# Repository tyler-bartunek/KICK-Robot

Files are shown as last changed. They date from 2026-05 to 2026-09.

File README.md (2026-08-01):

# The KICK Robot KICK Logo

&nbsp;
&nbsp;
_Democratizing robotics, one shoebox at a time_

The KICK (Kinematically Interchangeable Control Kit) Robot framework is an open-source platform designed to make learning about and development of mobile robotic systems accessible, modular, and affordable.

## Table of Contents
- [Repository Structure](#repository-structure)
- [The Wiki](#the-wiki)
- [Module Descriptions](#module-descriptions)
- [Hardware](#hardware)
  - [Printed Components and Module Fit](#printed-components-and-module-fit)
- [Future development](#future-development)
- [FAQ](#faq)
- [License](#license)

## Repository Structure
- `/hardware/` – STL and STEP files for 3D printing
- `/software/` – Code for the centralized controller (in progress), example firmware for modules, and hardware test scripts
- `/docs/` – Printing instructions, and additional reference material as it becomes available (PDF)
- `/images/` – Holds images used in this README, as well as some others throughout the repository
- `README.md` – You are here.

## The Wiki
Documentation for this project, including: 

- Part orientation and printer setting recommendations
- Assembly instructions
- Calibration and hardware validation protocols
- System-level descriptions
- and more

are being migrated to the [project wiki](https://www.github.com/tyler-bartunek/KICK-Robot/wiki) for ease of access
and navigation purposes. There's a lot that goes into this system, and it is only fitting that worthy documentation
would be quite extensive, requiring a wiki to track it all. 

## Module Descriptions
Here are a few of the modules under development at present for the KICK Robot. Once these modules are fully fleshed
out, a homebrew guide will be produced and added to the wiki.

1. Wheels: This module consists of DC motors and mecanum wheels, represents minimal functional example (systems integration in process).
2. Shoeshine: Offers quadrupedal motion through use of servomotors (Pending Initial Design)
3. HexaBox: Requires six mounts, offers six-legged locomotion through use of servomotors. (Pending Initial Design)

Note that each module type gets its own uint8_t identifier. Here are some urrently used ID's within KICK framework:

| ID | Module Type |
|----|---|
|0x00 | **Reserved**: No Connection |
|0x01 | Echo test functionality |
|0x02 | Mecanum Wheel Version A |
|0x03 | Mecanum Wheel Version B |
|0x04 | Quadruped Leg Version A |
|0x05 | Quadruped Leg Version B |

## Hardware

### Printed Components and Module Fit
Both STEP and STL files for all components to be printed are provided under the hardware directory, with directions for
the base hardware and wheels module provided in the wiki. As modules are added, printing directions specific
to those modules will be added. This system was prototyped using an Ender 3 V2 and Cura slicer using 
PLA+, with dimensions set to reflect typical tolerances for that printer with the intent of clearance fits with minimal play between 
mounting rails and modules.

## Software
Files for characterizing your specific motors and verifying basic hardware connections to the Pi, such as the ADC for 
battery level monitoring and custom SPI fanout board PCB, are provided within this repository, as well as the base
code for the picos/modules. Module code was developed using the Raspberry Pi Pico C++ SDK and uses CMake (C++17).

ROS code for the Raspberry Pi was developed using the ros:jazzy-core docker image, and is available on a [separate repository](https://github.com/tyler-bartunek/kick_pi) for direct download on your raspberry pi once finished. Raspberry 3b+ or better strongly encouraged, as the project was developed on a 3b+. 

### Philosophy, Parent Classes: Validation Ongoing, wiki articles available upon completion
While this is explained in greater detail in the [wiki](https://www.github.com/tyler-bartunek/KICK-Robot/wiki), provided here is a brief overview
for integration purposes. Overall, the goal is for users to be able to extend this framework to arbitrary module configurations. 

#### Configuration Class (ROS)
Within this project's underlay (not to be confused with the ROS underlay), there is a kickbrain package. This package has a nested package within it
called "configuration_files". The Configuration class is defined within this subpackage, and all kinematic calculations are predicated on the geometry_msgs.msg.Twist message type coming from the motion planner, with these velocities defined relative to the center of mass, presumed or actual. 

**All user-defined configurations must inherit from the Configuration parent class and have both a fetch_commands and compute_received method defined as following signatures:** 
```
def fetch_commands(self, vel_cmd: Twist, feedback) -> list:
```

This method takes the center of mass velocity command from the motion planning node, which uses the built-in geometry\_msgs.Twist topic message type and any feedback to compute new actuator commands. 

``` 
def compute_received(self, device_data) -> Twist:
```
This method takes the data received from the bus\_hub node and computes the forward kinematics for your configuration to build feedback. 

Once you have your configuration kinematics defined, you go to the \_\_init\_\_.py file within the configuration\_files directory and add the frozenset of module ids that can be used to recognize your configuration. Note that it does use a frozenset, so if you need X number of modules for a successful deployment, be sure to add that check to your custom configuration's class definition.

__**Note that 0x00 is reserved as the "no connection" module ID, so your frozenset will need to include it if any connection points on the harness are disconnected**__

_There is a possibility that you will need to modify it directly within the kickbot_node package and rebuild it using colcon build --packages-select to achieve desired behavior, but efforts will be made to allow you to develop your own configuration definitions in an overlay._

#### Module Class (Pico)
The microcontroller code for the picos is organized in the following folder structure:

1. kick_pico: **project root, make/build from here** <br>
   a. modules: Contains the Module parent class and any subclass definition cpp and h files <br>
   b. utils: Additional cpp and header files for achieving any functionality the modules require, such as SPI communication or quadrature encoder reading <br>
   c. main.cpp: driver script, creates the `pico_device` instance and calls its `run()` method repeatedly <br>

You define your custom module by adding a header and cpp file within the modules subdirectory, and be sure to add the relevant files to the CMakeLists.txt file within that subdirectory. The custom module class that you define **must** inherit from the Module base class, and must include a run method override that defines your module's behavior in response to received data from the Pi. That run method **must** call `this -> Transfer(data)`, where `data` is a short (uint16\_t) being sent back to the pi. 

Minimally viable example of a custom subclass header file:
```
#pragma once

#include "Module.h"

class MinimalExample : public Module {
    
    public:
        
        MinimalExample();

        void run() override;

        ~MinimalExample() = default;
};
```

If your module requires additional custom header files to function, these go under the utils subdirectory and you will in turn need to modify that CMakeLists.txt file.

For example, if you need to add something for the module to read an encoder that you've either written or cloned a library for named MyReallyCoolEncLib, you would modify the very first line of CMakeLists.txt file in utils to read:

```
add_library(utils STATIC SPITools.cpp MyReallyCoolEncLib.cpp)
```

assuming that your library has a cpp file defined for it.

Lastly, you modify line 18 of main.cpp to have the name of your new module type

```
#define MODULE_TYPE MinimalExample
```

**When you define your own module definitions they must inherit from the Module base class, have a unique uint8_t ID defined, and contain a run() method override.** A sync_callback() method override is optional, but recommended if the modules need to act in a coordinated fashion (as most do). Wiki article coming soon.  

## Future development
This project is still under development, and additional details such as synchronization and timing
requirements will be made available as they are validated. Current work is focused on validating the ROS setup and getting the Wheels Module ready to ``roll". 

## FAQ

1. Why shoeboxes?

>I had originally set out to make what essentially amounts to just the wheels module as a CAD and mechatronic portfolio piece.
Seeking to understand the design considerations, I started to immerse myself in literature surrounding mecanum wheel devices 
and discovered something that is in hindsight self-evident: different design decisions like the wheel spacing and orientation 
fundamentally alters the dynamics of the system and therefore influence control. Creating modular systems to explore the impact 
of these parameters was largely underexplored in what I found, so I set out to make my own. But I needed a good frame. Something
cheap and easy to deploy. As I looked around me, I saw an unused shoebox. And the KICK Robot was born. 

>Realistically any cardboard box will work, but at the time a shoebox seemed like the right size for what I set out to accomplish.

2. Why didn't you use \<insert fastener here\> to fasten the modules to the box?

>In the early days, I explored a number of different means for mounting the hardware to the box. The current design for mounting
hardware to the box solves two problems simultaneously: the first is that of establishing a secure connection with minimal
assembly complexity, the second is offering a path for routing the wires from inside the box to the modules on the outside.

3. Doesn't the act of cutting into the box limit the reusability of a single box to test multiple design parameters?

>Yes, as do other adhesives that have enough strength to reliably anchor the hardware to the outside of the box. 

## License
As of 19 November, 2025, this project is licensed under the terms of the [Apache License-2.0](LICENSE). Software provided prior 
to this date was licensed under the terms of the MIT license, and includes the content of the directory 
`/software/Hardware Characterization/Wheels Module`. The transition to the Apache License-2.0 is to reflect that this repository
contains more than just software. 

This project also uses PyMC in the motor characterization code for the Wheels module. PyMC is also licensed under the terms
of the [Apache License-2.0](LICENSE), and also includes software licensed under the MIT license. A notice is provided in the
main directory of this repository, to underline this point and include the necessary copy of the MIT license for portions 
covered by that license.

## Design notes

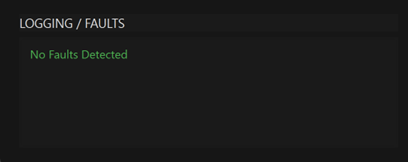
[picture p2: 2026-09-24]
images/wiki/KICK-GUI-logging.png

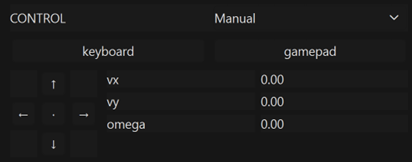
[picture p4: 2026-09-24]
images/wiki/KICK-GUI-control.png

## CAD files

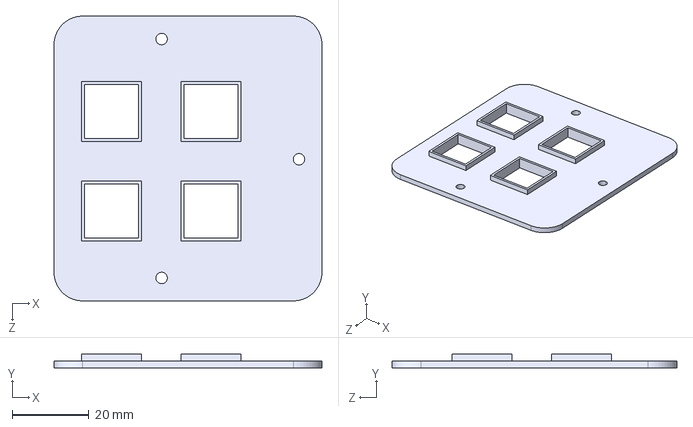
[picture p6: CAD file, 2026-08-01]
Hardware/Attachment Points/STEPs/BasePlate_Ext_Middle.STEP
70.0 x 3.60 x 74.4 mm

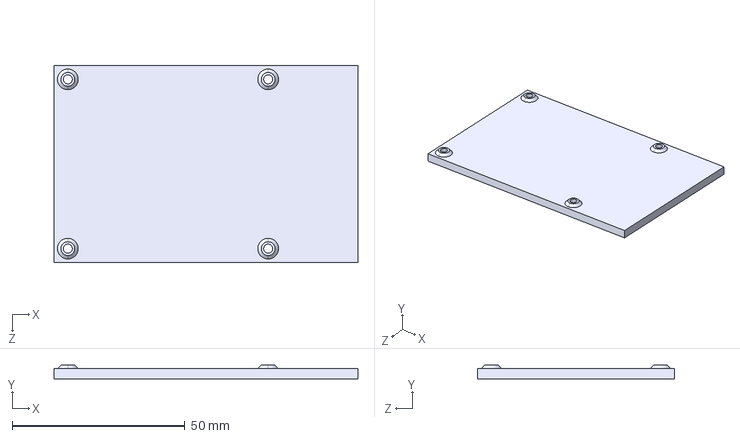
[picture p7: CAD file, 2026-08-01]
Hardware/Central Electronic Mounts/STEPs/Rpi_3b_mount.STEP
88.0 x 4.00 x 57.0 mm

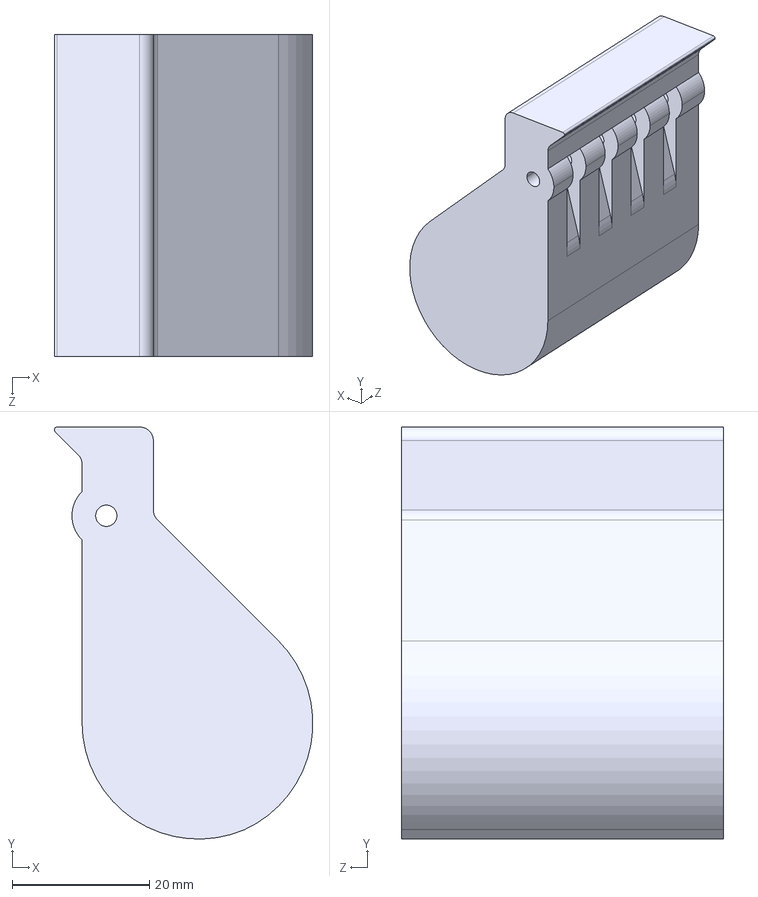
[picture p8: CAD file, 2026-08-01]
Hardware/Wheel Module/STEPs/Handle.STEP
37.6 x 60.1 x 47.0 mm

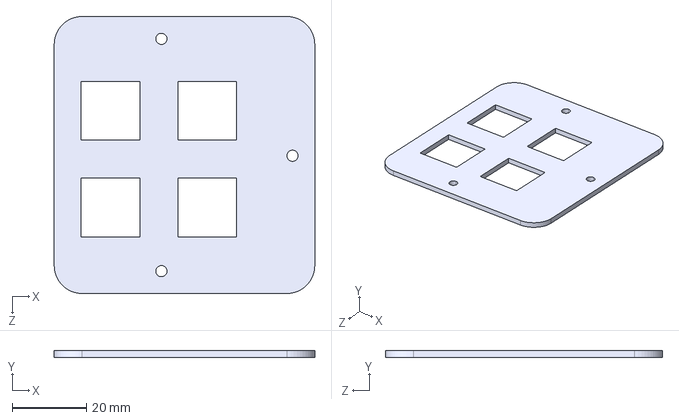
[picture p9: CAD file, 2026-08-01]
Hardware/Attachment Points/STEPs/BasePlate_Int_Middle.STEP
70.0 x 1.80 x 74.4 mm

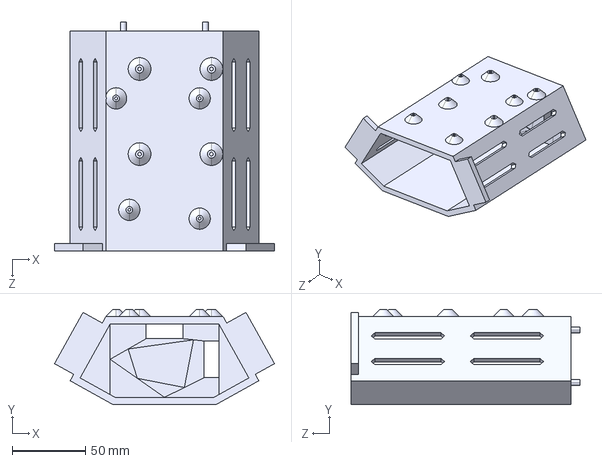
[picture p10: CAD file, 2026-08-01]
Hardware/Central Electronic Mounts/STEPs/Central_Electronics_Mount.STEP
150.0 x 65.0 x 156.0 mm

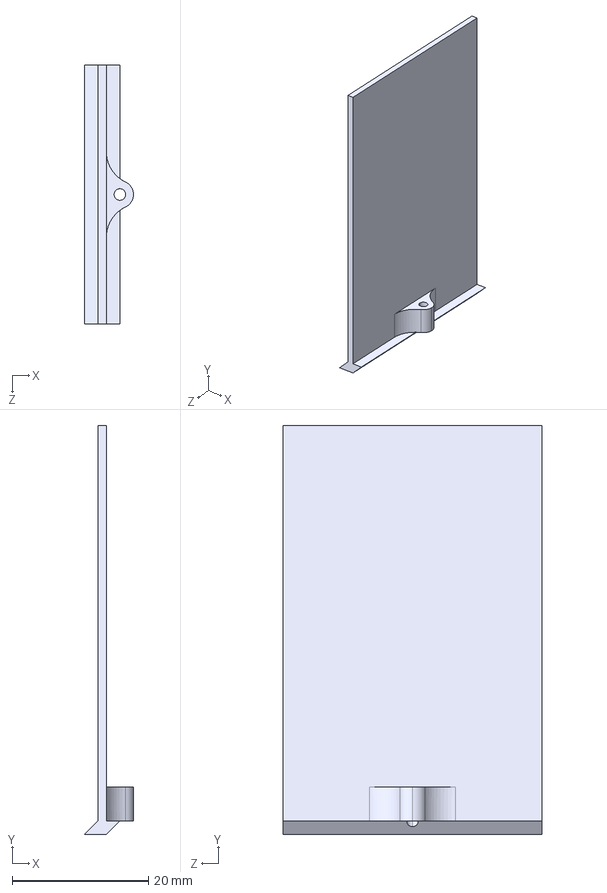
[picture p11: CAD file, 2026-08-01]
Hardware/Wheel Module/STEPs/Pico_Shield.STEP
7.20 x 60.0 x 38.0 mm

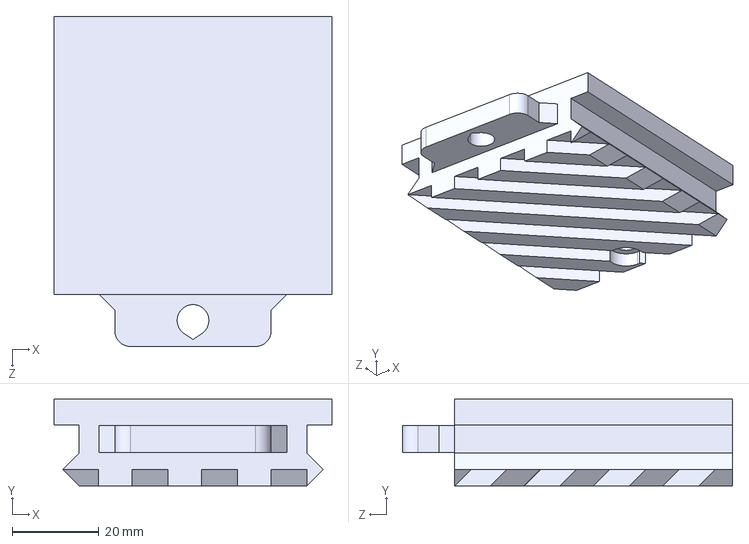
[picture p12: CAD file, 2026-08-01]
Hardware/Attachment Points/STEPs/BaseMount.STEP
64.0 x 20.0 x 76.0 mm

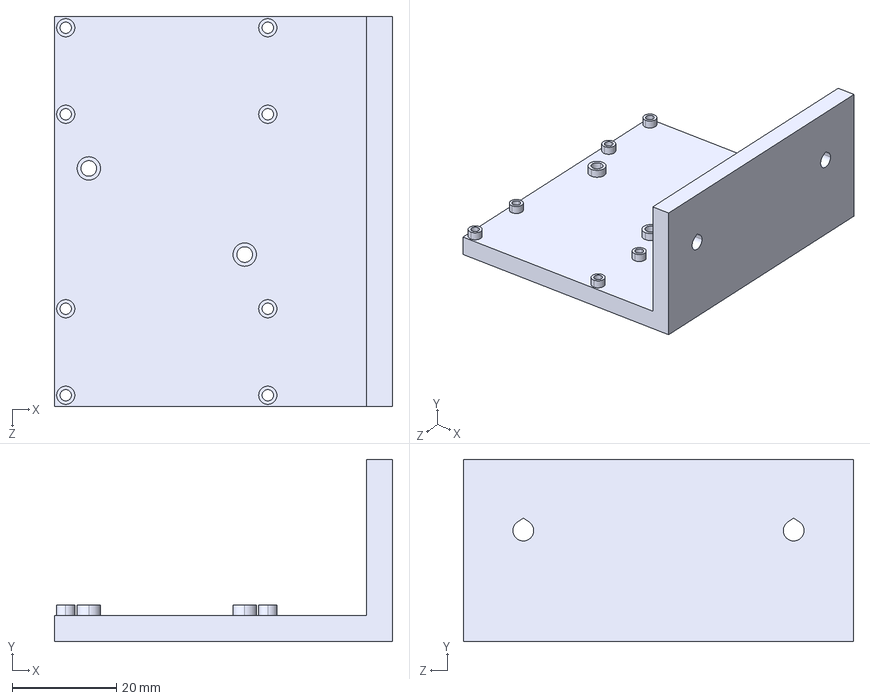
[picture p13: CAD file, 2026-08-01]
Hardware/Central Electronic Mounts/STEPs/Buck_Mount.STEP
65.0 x 35.0 x 75.0 mm

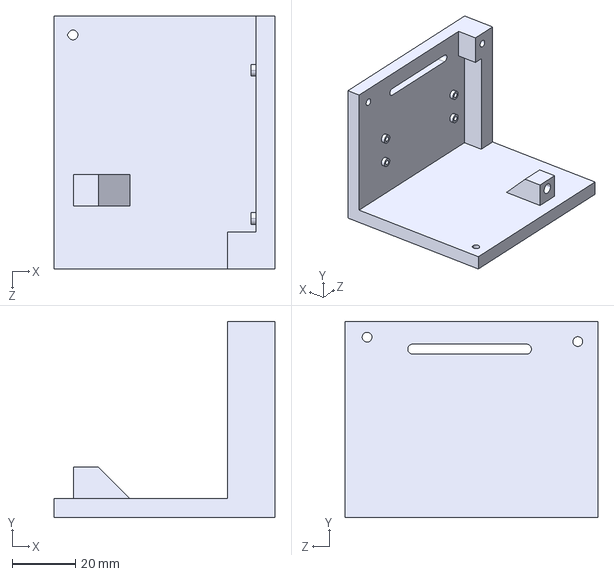
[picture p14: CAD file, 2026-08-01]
Hardware/Wheel Module/STEPs/Motor_Mount_Side_Bottom.STEP
70.0 x 62.2 x 80.2 mm

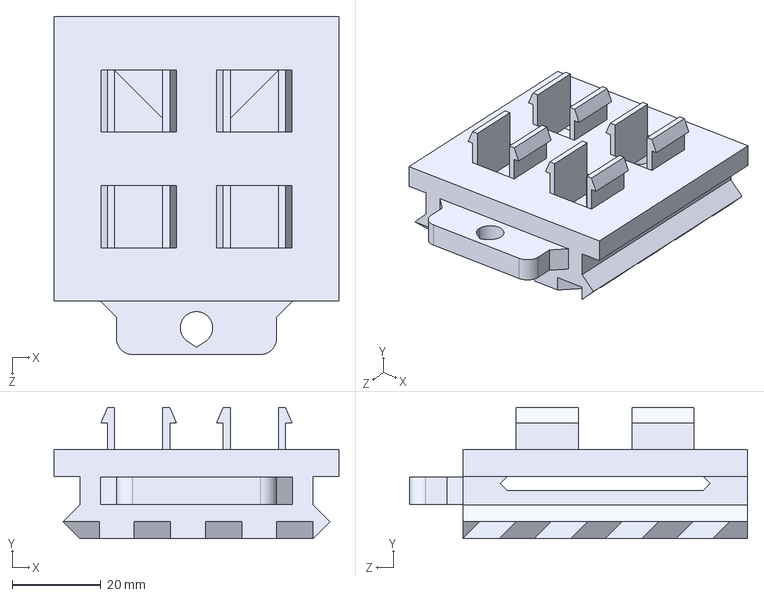
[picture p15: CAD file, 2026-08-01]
Hardware/Attachment Points/STEPs/BaseMount_Clips.STEP
64.0 x 29.5 x 76.0 mm

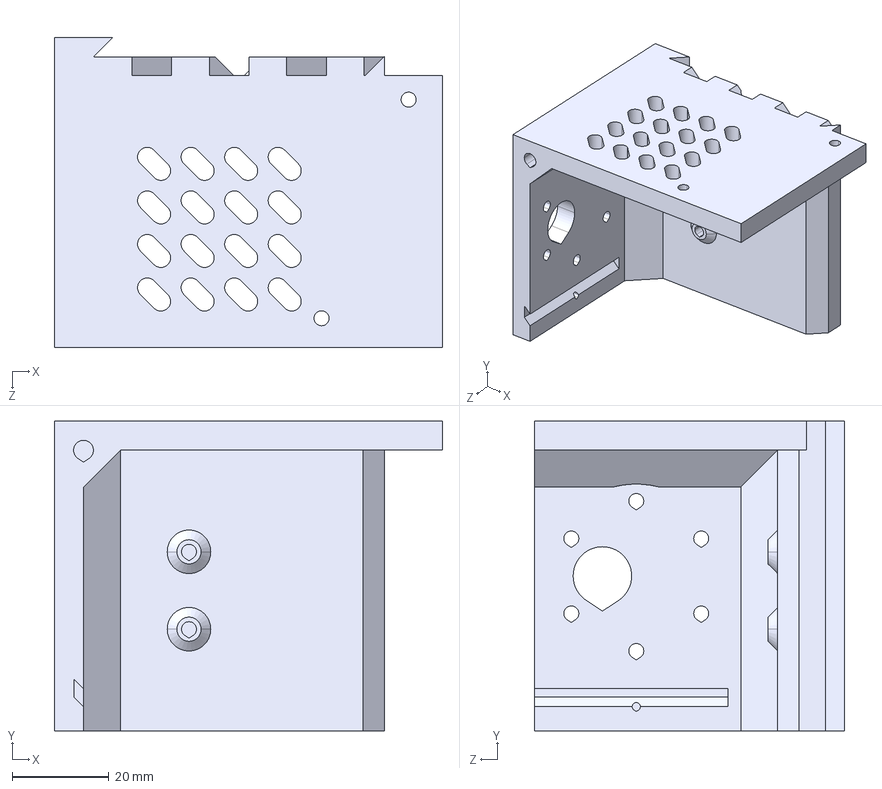
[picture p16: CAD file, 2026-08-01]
Hardware/Wheel Module/STEPs/Motor_Mount_Attachment.STEP
80.2 x 64.0 x 64.0 mm

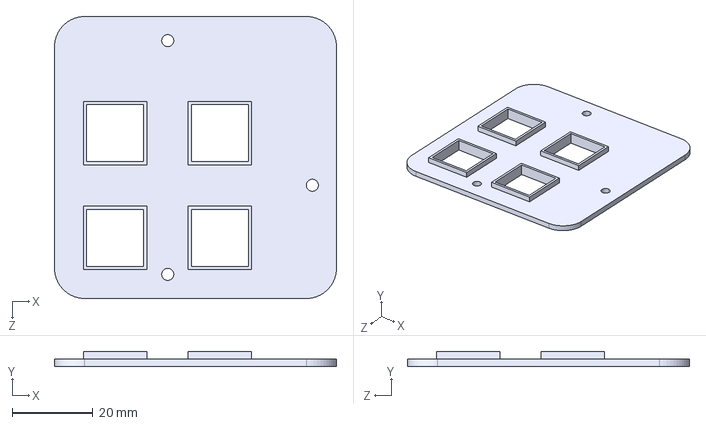
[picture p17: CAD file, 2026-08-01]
Hardware/Attachment Points/STEPs/BasePlate_Ext_Corner.STEP
70.0 x 3.60 x 70.0 mm

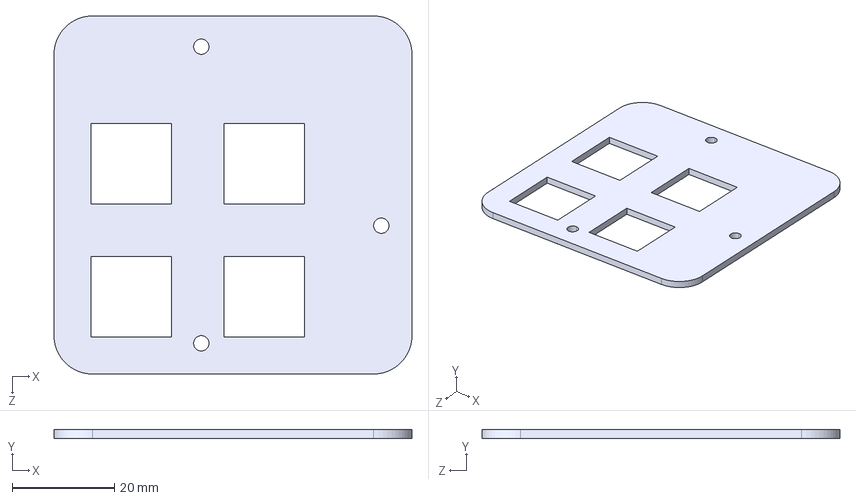
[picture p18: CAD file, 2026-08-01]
Hardware/Attachment Points/STEPs/BasePlate_Int_Corner.STEP
70.0 x 1.80 x 70.0 mm

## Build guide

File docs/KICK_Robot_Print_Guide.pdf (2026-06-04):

# KICK Robot

# Quick-Start Excerpt: Printing Guide

## Revision Date: June 3, 2026

# Contents

## Downloading Files

These instructions are written for a Windows 10 computer, though the basic principles should transfer reasonably well to other platforms like Mac and Linux operating systems.

## Installing Git

Open a web browser and navigate to https://git-scm.com/ and go to the downloads page. Follow their posted directions, and once installation is complete you will be ready to get started.

## Cloning the Repository

Once git is installed, open a terminal and navigate to the directory where you would like to save the project files. If you know how to do this already, you can skip the steps detailing this process.

### Navigating to Desired Directory using Command Prompt

You do this on Windows by going to the search bar and typing “cmd”, you should see something like the following come up, though the specifics will depend on the software you have installed on your device.

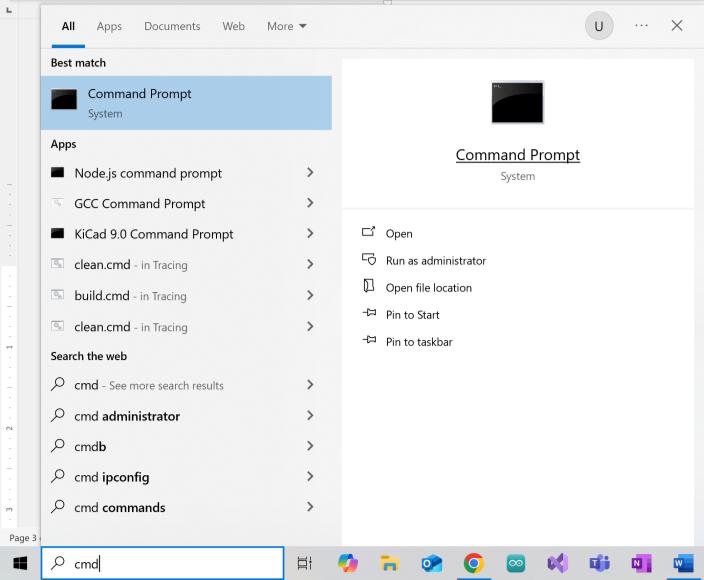
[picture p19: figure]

Figure 1. This screenshot illustrates opening the Command Prompt terminal from the Windows search bar.

1. Open Command Prompt and you should see a terminal window open. Odds are good that your desired location is going to be somewhere off the user directory, which is what Command Prompt opens to by default. In this example, the desired directory is a desktop folder created specifically for the user’s GitHub repositories.

2. Type cd ./<name of target directory> In the example provided in Figure 2, the full command is cd ./Desktop/My Stuffs/Git Repos/

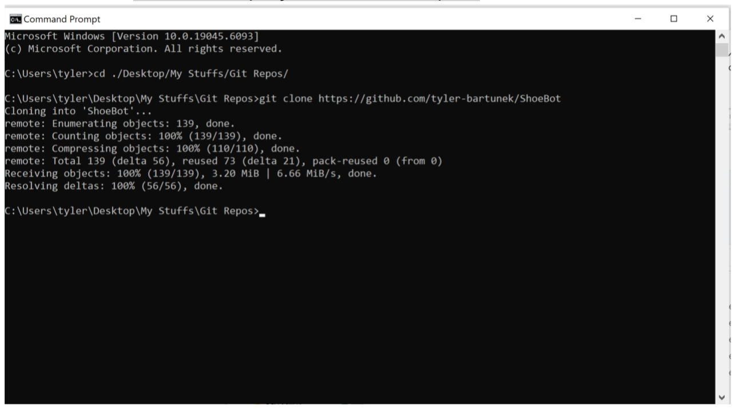
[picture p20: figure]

Figure 2. The complete set of commands necessary to get a clone of the repository onto your local device. The repository has been renamed since this was generated, disregard the ShoeBot mention.

### Finally Cloning the Repository

Now that you are set up with git and are have navigated to the location you want the files to download, it is time to download a copy of the files into this location. Type or copy-paste

git clone https://github.com/tyler-bartunek/KICK-Robot

into your terminal. The download process should run automatically and once finished you should have a new folder in that location named KICK-Robot. Note that it may prompt you to sign in to github, which may entail setting up an account.

If this step has finished successfully, then you can now close the Command Prompt and continue navigation through the File Explorer like usual.

## Printing Instructions for Hardware

Navigate to the Hardware directory of the repository. In it, you will find folders for

- Attachment Points
- Central Electronic Mounts

- SPI Hub PCB KiCad files
- Wheel Module.

This section will concern all of these folders except the SPI Hub folder, as that information is for an optional component that is not 3D-printed. Every folder that has parts to be 3D-printed will contain folders for STEP and STL files, with the former provided in the event that you need to modify the base design of any of the components.

All parts were printed using PLA+ during the design process with:

- 0.4 mm nozzle and line width
- 20% infill (cubic)
- Tree supports as applicable
- 2 wall lines
- 50 mm/s print speed

To maximize print time efficiency, it is strongly recommended to print multiple components at once. For example, printing half of the rail pieces in a batch and all the motor mount attachments in another batch instead of each rail and motor mount attachment piece individually. With these print settings it was not uncommon to encounter 2+ day prints on an Ender 3V2 running Marlin. So again, the recommendation is to print as many things simultaneously as possible.

In total, you will need to print the following to match the development setup:

- 6 Base Mount Clips
- 4 Base Mounts
- 4 Internal Corner Plates
- 2 Internal Middle Plates
- 4 External Corner Plates
- 2 External Middle Plates
- 4 Motor Mount Attachments
- 4 Motor Mount Side Bottoms
- 4 Handles
- 4 Pico Shields
- 1 Central Electronics Mount
- 1 Buck Converter Mount
- 1 Raspberry Pi 3b+ Mount
- 4 Spacers (print last)

For best results, print at a 0.1 mm layer height as this will allow in Cura for steeper overhangs and fewer supports.

## Attachment Points

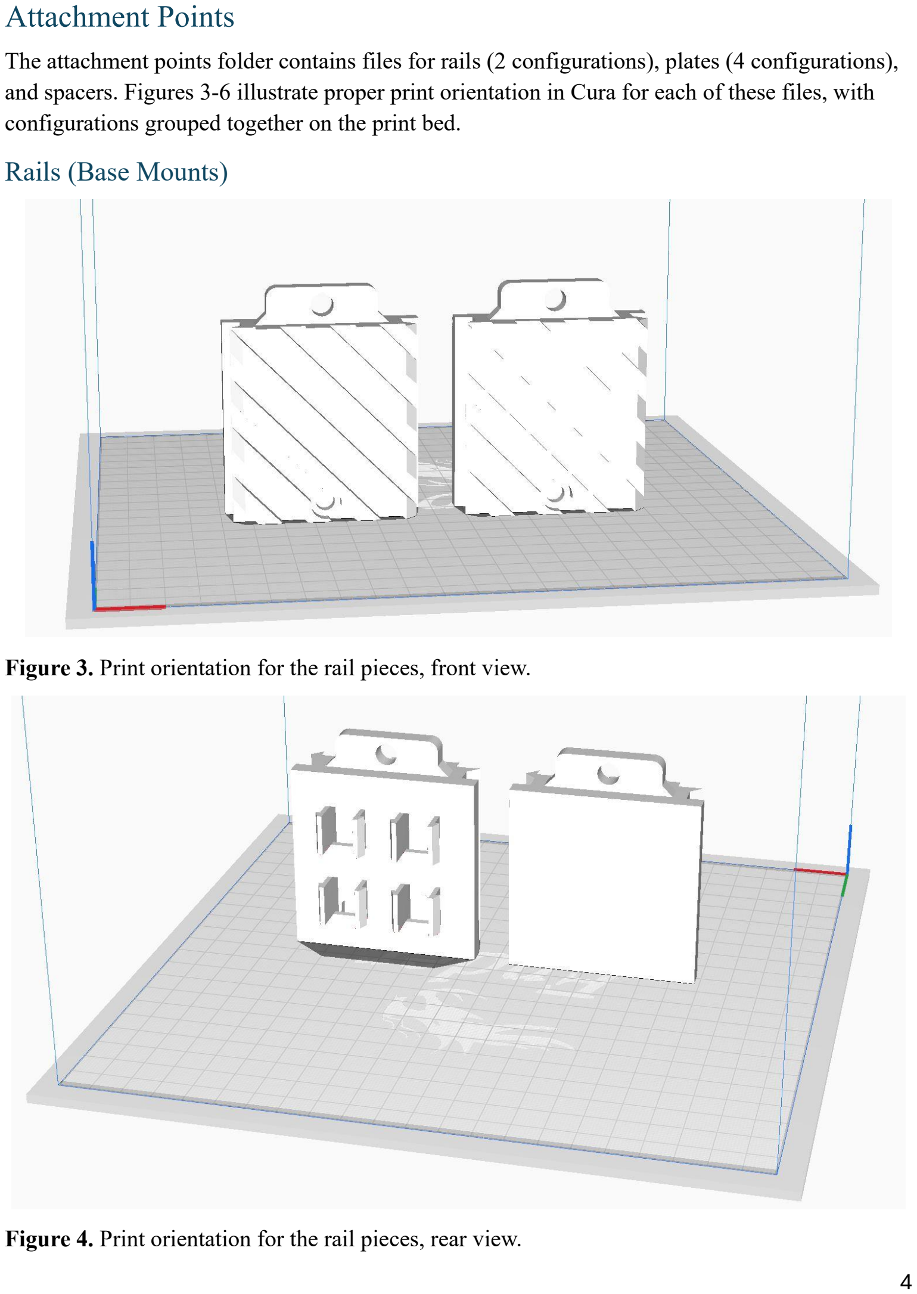
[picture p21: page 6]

The attachment points folder contains files for rails (2 configurations), plates (4 configurations), and spacers. Figures 3-6 illustrate proper print orientation in Cura for each of these files, with configurations grouped together on the print bed.

### Rails (Base Mounts)

Figure 3. Print orientation for the rail pieces, front view.

Figure 4. Print orientation for the rail pieces, rear view.

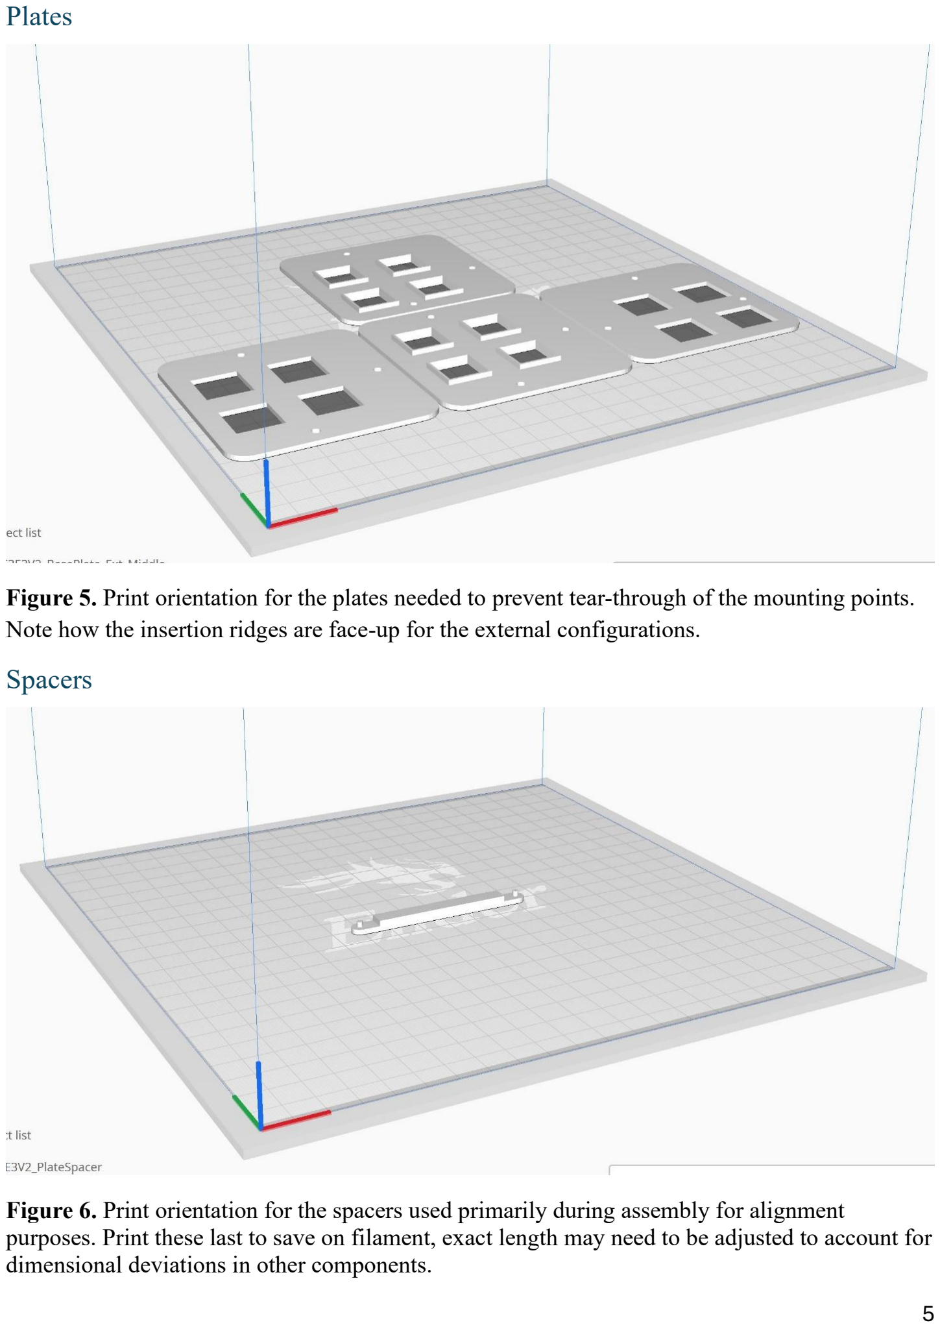
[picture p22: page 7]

### Plates

Figure 5. Print orientation for the plates needed to prevent tear-through of the mounting points. Note how the insertion ridges are face-up for the external configurations.

### Spacers

Figure 6. Print orientation for the spacers used primarily during assembly for alignment purposes. Print these last to save on filament, exact length may need to be adjusted to account for dimensional deviations in other components.

## Central Electronics Mount

### Central Mount

## Pending Redesign

Figure 7. Print orientation for the central electronics mount.

### Buck Attachment Point

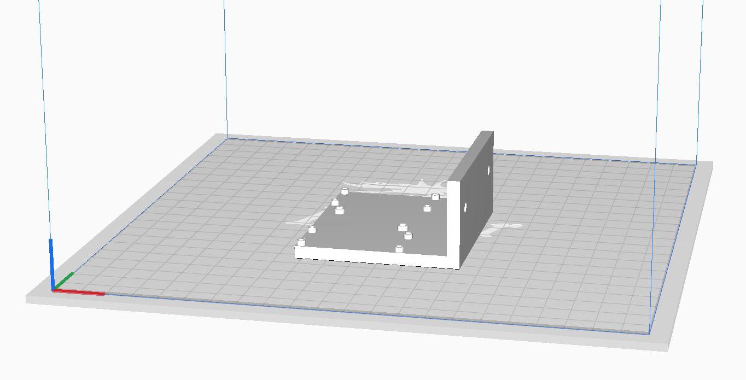
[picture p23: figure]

Figure 8. Print orientation for the buck converter mounting point, with the raised portions oriented upwards.

## Wheels Module Hardware

### Motor Mount Attachment

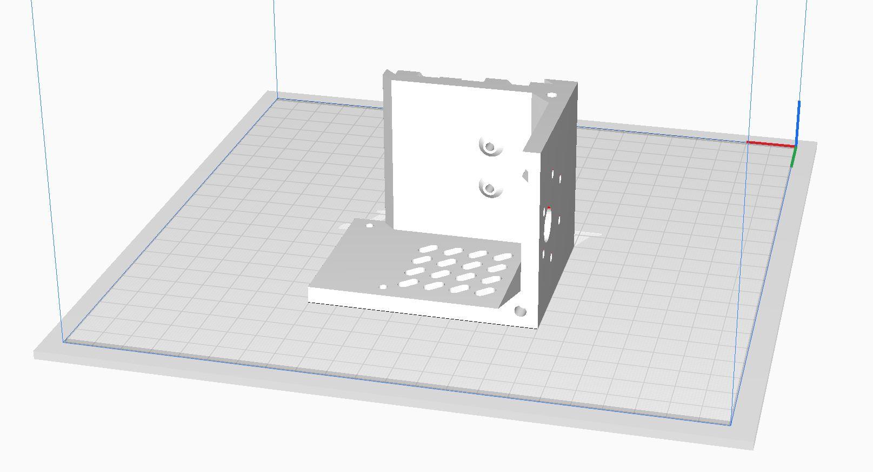
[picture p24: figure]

Figure 10. Print orientation for the motor mount attachment piece, illustrating that ventilation slots print on the bottom face.

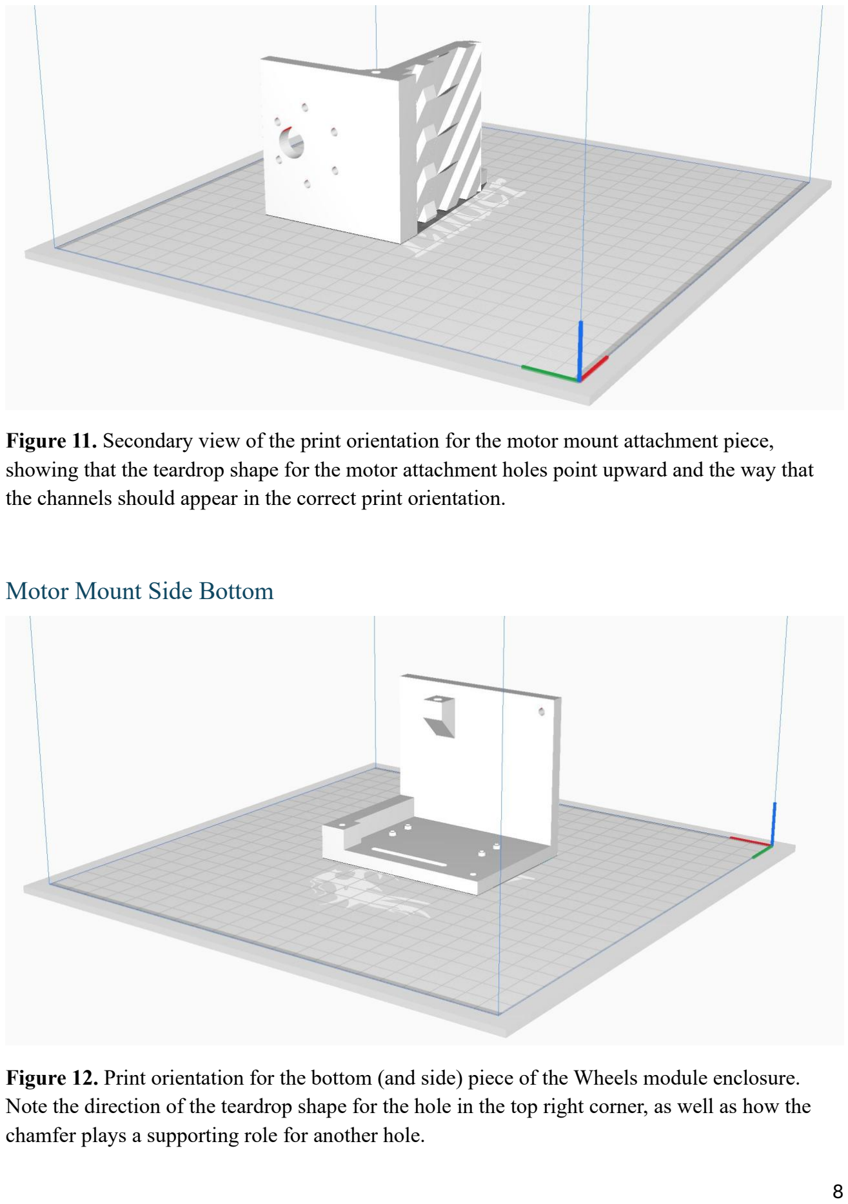
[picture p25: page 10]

Figure 11. Secondary view of the print orientation for the motor mount attachment piece, showing that the teardrop shape for the motor attachment holes point upward and the way that the channels should appear in the correct print orientation.

### Motor Mount Side Bottom

Figure 12. Print orientation for the bottom (and side) piece of the Wheels module enclosure. Note the direction of the teardrop shape for the hole in the top right corner, as well as how the chamfer plays a supporting role for another hole.

### Handle

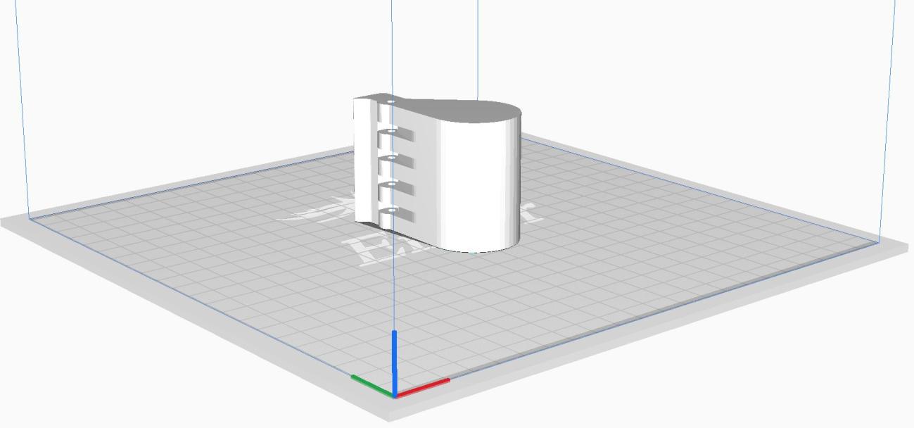
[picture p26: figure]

Figure 13. Print orientation for the handle of the wheels module. Note that care should be taken to ensure that the gaps for the springs are cleaned out well enough for the springs to fit, as supports will want to fill this space.

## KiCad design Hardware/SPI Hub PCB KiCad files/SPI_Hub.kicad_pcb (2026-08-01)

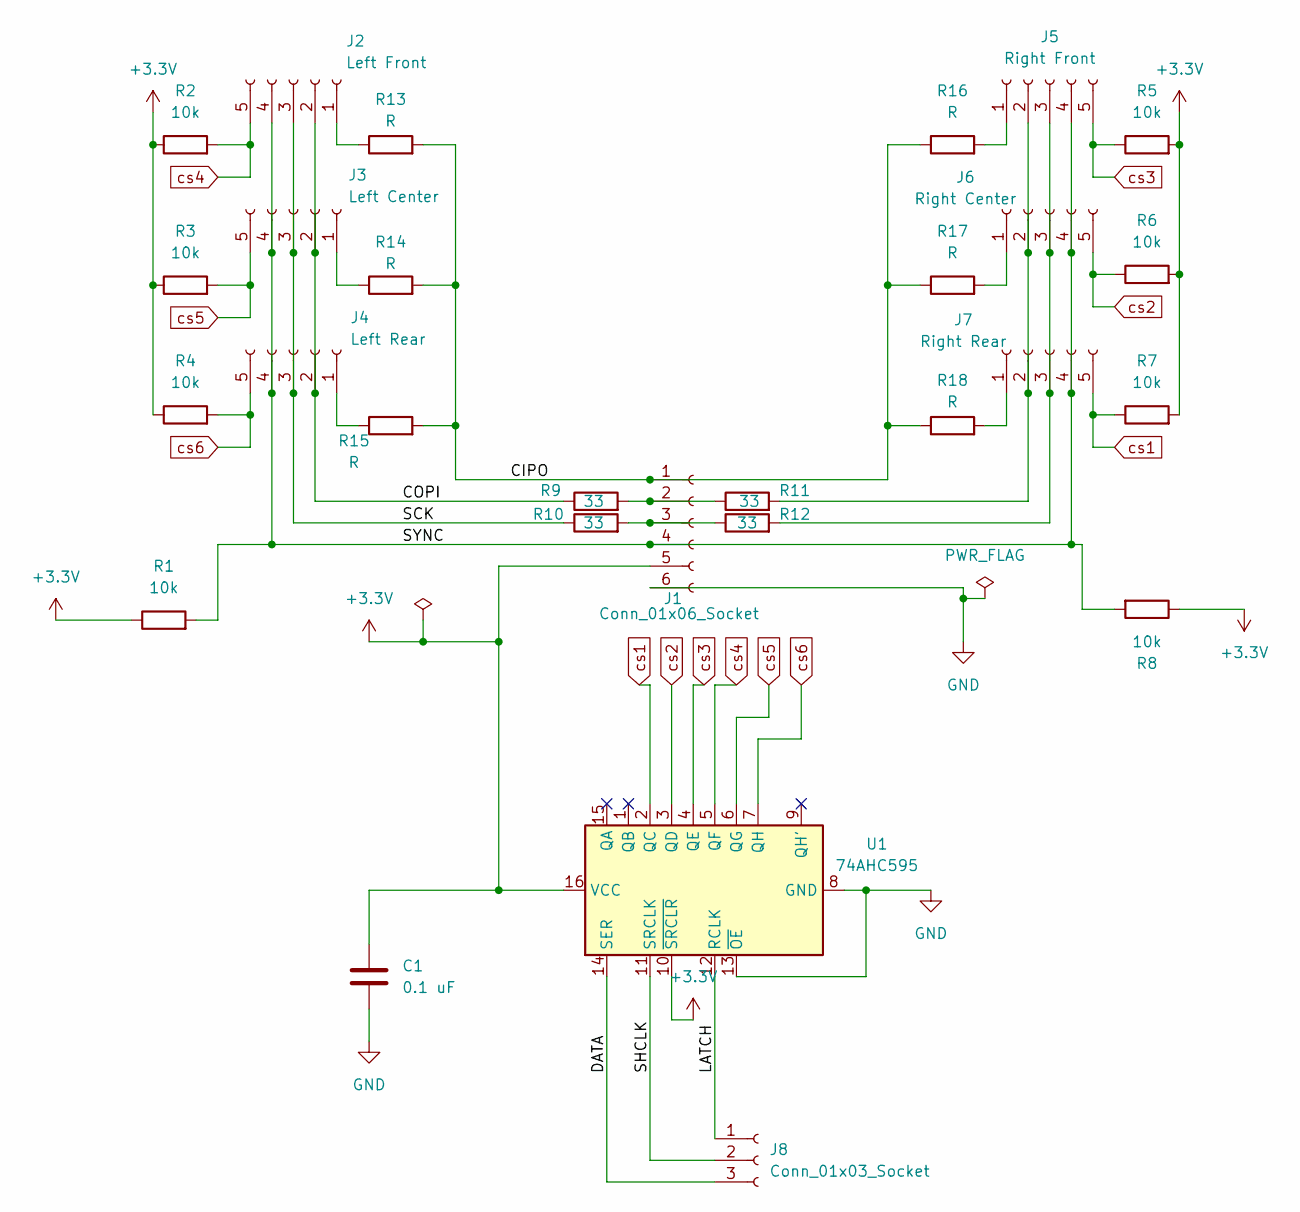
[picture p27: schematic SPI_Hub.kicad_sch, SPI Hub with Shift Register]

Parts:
C1: 0.1 uF; C_0805_2012Metric_Pad1.18x1.45mm_HandSolder
J1: Conn_01x06_Socket; JST_XH_B6B-XH-A_1x06_P2.50mm_Vertical
J2: Left Front; JST_XH_B5B-XH-A_1x05_P2.50mm_Vertical
J3: Left Center; JST_XH_B5B-XH-A_1x05_P2.50mm_Vertical
J4: Left Rear; JST_XH_B5B-XH-A_1x05_P2.50mm_Vertical
J5: Right Front; JST_XH_B5B-XH-A_1x05_P2.50mm_Vertical
J6: Right Center; JST_XH_B5B-XH-A_1x05_P2.50mm_Vertical
J7: Right Rear; JST_XH_B5B-XH-A_1x05_P2.50mm_Vertical
J8: Conn_01x03_Socket; JST_XH_B3B-XH-A_1x03_P2.50mm_Vertical
R1, R2, R3, R4, R5, R6, R7, R8: 10k; R_0805_2012Metric_Pad1.20x1.40mm_HandSolder
R9, R10, R11, R12: 33; R_0805_2012Metric_Pad1.20x1.40mm_HandSolder
R13, R14, R15, R16, R17, R18: R; R_0805_2012Metric_Pad1.20x1.40mm_HandSolder
U1: 74AHC595; DIP-16_W7.62mm_Socket

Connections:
+3.3V: C1.1, J1.5, R1.1, R2.1, R3.1, R4.1, R5.2, R6.2, R7.2, R8.1, U1.10 (~SRCLR), U1.16 (VCC)
/CIPO: J1.1, R13.2, R14.2, R15.2, R16.1, R17.1, R18.1
/COPI: J2.2, J3.2, J4.2, R9.1
/DATA: J8.3, U1.14 (SER)
/LATCH: J8.1, U1.12 (RCLK)
/SCK: J2.3, J3.3, J4.3, R10.1
/SHCLK: J8.2, U1.11 (SRCLK)
/SYNC: J1.4, J2.4, J3.4, J4.4, J5.4, J6.4, J7.4, R1.2, R8.2
GND: C1.2, J1.6, U1.8 (GND), U1.13 (~OE)
unnamed: J1.2, R9.2, R11.1
unnamed: J1.3, R10.2, R12.1
unnamed: J2.1, R13.1
unnamed: J3.1, R14.1
unnamed: J4.1, R15.1
unnamed: J5.1, R16.2
unnamed: J5.2, J6.2, J7.2, R11.2
unnamed: J5.3, J6.3, J7.3, R12.2
unnamed: J6.1, R17.2
unnamed: J7.1, R18.2
cs1: J7.5, R7.1, U1.2 (QC)
cs2: J6.5, R6.1, U1.3 (QD)
cs3: J5.5, R5.1, U1.4 (QE)
cs4: J2.5, R2.2, U1.5 (QF)
cs5: J3.5, R3.2, U1.6 (QG)
cs6: J4.5, R4.2, U1.7 (QH)

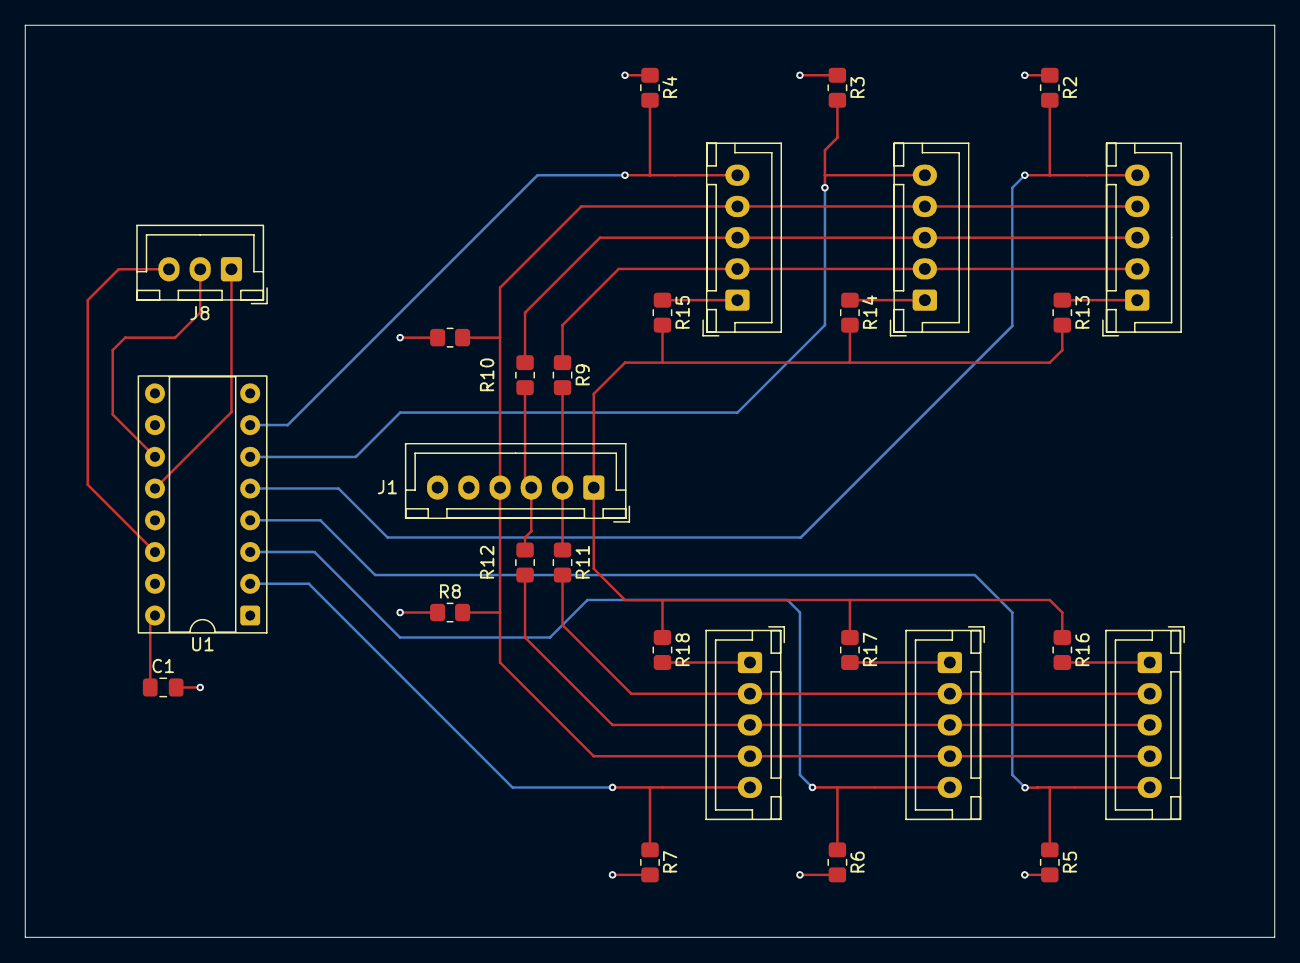
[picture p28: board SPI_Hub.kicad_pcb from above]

Board: 4 copper layers, 100.0 x 73.0 mm, 28 parts (0 on the bottom side), 25 nets.

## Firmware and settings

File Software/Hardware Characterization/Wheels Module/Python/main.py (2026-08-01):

"""
MotorCharacterize_SpeedBoost
"""

#Standard library imports: basic functionality
import os
import os.path as pth
import pandas as pd
import numpy as np

#Serial communication and post-processing
from SerialStreamParser import GatherAndStore
from PostProcessing import MotorData, ParseMotorData, ReshapeMotorData, GetTimesAndVoltages

#generating unique filename for date and time
from datetime import datetime

#MCMC code and simulations
from mcmc_simulator import HierarchicalModel, InitializeSimulations, RunBlocks, RunCommandForParams, PackOutputList
from StateModels import MotorModel

#Kalman Filter, MLE fitting
from filters import EWMA, StateObserver

#Plotting, as well as loading in trace data from MCMC
import matplotlib.pyplot as plt
import arviz as az 

#Set the random seed (done after bayesian and monte carlo fitting procedure)
np.random.seed(0)
    

#############################################################################################################################
############################################# Helper/Packing Functions ######################################################
#############################################################################################################################   


def WriteParamsToFile(param_dict:dict[str,float], file) -> None:
    for param in param_dict.keys():
        file.write("{} = {}\n".format(param, param_dict[param]))

    file.write("\n")

def OpenParamsFromFile(filename:str, param_keys:list[str]) -> tuple[dict[str, float], list[dict[str,float]]]:

    params_list_motors = []
    with open(filename, 'r') as file:

        chunks = file.read().split('\n\n')
        for chunk in chunks:
            lines = chunk.split('\n')

            params_dict = {param:0 for param in param_keys}

            for line in lines[1:]:

                key_value_separation = line.split(' = ')
                try:
                    params_dict[key_value_separation[0]] = float(key_value_separation[1].strip())
                except KeyError:
                    raise KeyError("Mismatch between expected keys and zeroth value of key_value_separation")

            if 'Motor' in lines[0]:
                params_list_motors.append(params_dict)
            
            elif 'Global' in lines[0]:
                global_params_dict = params_dict.copy()
            else:
                pass
    
    return global_params_dict, params_list_motors
                
            
#############################################################################################################################
######################################################## Main ###############################################################
#############################################################################################################################
def main():

    #Serial communication variables
    COM_PORT = "COM3"
    BAUD_RATE = 230400

    time_cutoff = 800 #Record for 800 seconds

    #File naming information, timestamps each file it creates to prevent accidental overwrites
    motor = 'C'
    block_number = 1
    date_info = datetime.now()
    mmddyyyy = "{}{}{}_{}{}".format(date_info.month, date_info.day, date_info.year,date_info.hour, date_info.minute)

    #First line is for general fitting data files, second for filter testing
    data_filename = "motor_data_romeo_Motor{}_Block_{}_{}".format(motor, block_number, mmddyyyy)
    # data_filename = "motor_data_romeo_Motor{}_{}".format(motor, mmddyyyy)

    #First line is for general fitting data files, second for filter testing
    data_folder = pth.join(pth.dirname(__file__), "data/RCBD_Trials")
    # data_folder = pth.join(pth.dirname(__file__), "data/Disturbance_Tests")

    #lists of commands, to be used in plotting and processing steps
    multi_speed_commands = [31, 63, 95, 127, 159, 191, 223, 255]

    #Flags that control what the program is doing: collecting data, providing early visualizations, or preprocessing data
    collecting_data = False
    plot_raw_data = False
    preprocess_data = False

    #Model identification
    mcmc_ready = False
    compute_nominal_params = False

    #Filter tuning 
    tune_filter = True

    if collecting_data:

        GatherAndStore(COM_PORT, BAUD_RATE, time_cutoff, data_filename)
        
    if plot_raw_data:

        multi_speed_files = os.listdir(data_folder)
        MultiData = [MotorData(cell, filepath=data_folder) for cell in multi_speed_files]

        #Plot time vs PWM and Run number for data to check if we are cycling through commands correctly
        MultiData[0].plot('Time','Position')
        plt.show()

    if preprocess_data:

        multi_speed_files = os.listdir(data_folder)
        MultiData = [MotorData(cell, filepath=data_folder) for cell in multi_speed_files]
        
        aggregated_data = ParseMotorData(MultiData, multi_speed_commands)

        aggregate_data_path = pth.join(pth.dirname(__file__), "data")
        aggregated_data.to_csv(pth.join(aggregate_data_path, "Aggregate_Motor_Data_RCBD.csv"), index = False)
    
    if mcmc_ready:

        #Load in the datset
        aggregate_data_path = pth.join(pth.dirname(__file__), "data")
        aggregated_data = pd.read_csv(pth.join(aggregate_data_path, "Aggregate_Motor_Data_RCBD.csv"))

        #Instantiate the model
        h_model = HierarchicalModel(aggregated_data)
        #Fit the model
        h_model.fit(sd_multiplier=3)

        #If the model ran without divergences, save result
        if h_model.trace.sample_stats['diverging'].sum() == 0:
            h_model.trace.to_netcdf("data/Accepted_trace.nc")

        #Summarize fitted model
        print(az.summary(h_model.trace, var_names=["R", "K", "b", "c", "J"], round_to = 4))
        print(az.summary(h_model.trace, var_names = ["R_m", "K_m", "b_m", "c_m", "J_m"]))

        #Trace plot
        az.plot_trace(h_model.trace, var_names = ["R", "K", "b", "c", "J"], legend=True)
        plt.show()

        #Plot pairs of group and motor parameters
        az.plot_pair(h_model.trace, var_names = ["R", "R_m"], kind="kde", divergences = True)
        az.plot_pair(h_model.trace, var_names = ["K", "K_m"], kind="kde", divergences = True)
        az.plot_pair(h_model.trace, var_names = ["b", "b_m"], kind="kde", divergences = True)
        az.plot_pair(h_model.trace, var_names = ["c", "c_m"], kind="kde", divergences = True)
        az.plot_pair(h_model.trace, var_names = ["J", "J_m"], kind="kde", divergences = True)
        plt.show()

    if compute_nominal_params:

        #Prepare to write the parameters to a file
        param_file = "data/parameters.txt"
        f = open(param_file, 'w')

        #Set the number of simulations and initialize
        num_sims = 100
        motors, blocks, runs, params_global, params_motor_list, MultiDataReshape = InitializeSimulations("data/Aggregate_Motor_Data_RCBD.csv",
                                                                                                         "data/Accepted_trace.nc", num_sims= num_sims)

        #Run through the motors and get simulations for each block at command 255
        command = 255
            
        #Instantiate global-level model
        global_model = MotorModel(params_global)

        global_idx_stack = []
        
        for id, motor in enumerate(motors):
            
            #Instantiate global-level model
            motor_model = MotorModel(params_motor_list[id])

            motor_ind_idx_stack = []

            models = [global_model, motor_model]

            print("Simulating motor {}".format(motor))
            f.write("Motor {}\n".format(motor))

            run_command = lambda global_out_stack, motor_out_stack, models, data, sr_values, run:RunCommandForParams(global_out_stack, motor_out_stack, models, data, sr_values, run, command)
            RunBlocks(global_idx_stack, motor_ind_idx_stack, models, motor, blocks, runs, MultiDataReshape, multi_speed_commands, run_command)

            best_motor_params = PackOutputList(motor_ind_idx_stack, for_params = True, dict_to_pattern = params_motor_list[id])
            WriteParamsToFile(best_motor_params, f)
            print("...done.")

        print("Simulations finished, no more motors.")
        global_params_dict = PackOutputList(global_idx_stack, for_params=True, dict_to_pattern = params_global)
        f.write("Global Model\n")
        WriteParamsToFile(global_params_dict, f)

        f.close()

    if tune_filter:

        #Load my global and motor-level parameters
        params_global, params_motor_list = OpenParamsFromFile("data/parameters.txt", ["R", "K", "b", "c", "J"])

        #Load in my test data
        data_folder = pth.join(pth.dirname(__file__), "data/Disturbance_Tests")
        test_data = [MotorData(cell, filepath = data_folder) for cell in os.listdir(data_folder)]

        #Define the motor labels, and number of runs
        motors = ['A', 'B', 'C', 'D']
        runs = list(range(1,6))

        #Reshape my motor test data into a dict
        test_data_reshape = {motor:[] for motor in motors}
        for data in test_data:
            filename_segmented = data.filename.split('_')
            motor_label = filename_segmented[3][-1]
            if motor_label in motors:
                test_data_reshape[motor_label].append(data)


        #Create the filepath for the observer data plot figures to go
        #Filepath(s) for saving plots
        plot_path = pth.join(pth.dirname(__file__), "filter plots")
        speed_plot_path = pth.join(plot_path, "speed")

        #make the path if it doesn't exist
        if not pth.exists(plot_path):
            #Specifically make the path to position vs speed data
            os.mkdir(plot_path)
            os.mkdir(speed_plot_path)

        #Instantiate the filter
        alpha = 0.01 #filter gain, higher numbers indicate more trust in new measurements
        filter = EWMA(alpha)

        for run in runs:

            for command in multi_speed_commands:

                #Create subplots with labels, appropriate size (10x7 inches)
                fig_speed, ax_speed = plt.subplots(2,2)
                fig_speed.set_size_inches(10,7) 

                #Set overall title
                fig_speed.suptitle("Speeds for Run = {}, Command = {} \n alpha = {}".format(run, command, alpha))

                for id, motor in enumerate(motors):

                    row_idx = id // 2
                    col_idx = id - (row_idx * 2)

                    sr_values = test_data_reshape[motor][0].get_step_windows(multi_speed_commands)

                    #Extract observed_states
                    times = sr_values[run][command]['Time'].values
                    positions = sr_values[run][command]['Position'].values
                    speed_init_compute = np.diff(positions) / np.diff(times)
                    speeds = np.concatenate([[0], speed_init_compute])

                    #Set title
                    ax_speed[row_idx, col_idx].set_title(motor)

                    #Enable grid lines
                    ax_speed[row_idx, col_idx].grid(True)

                    #Set x and y labels on outside edge
                    if col_idx == 0:
                        ax_speed[row_idx, col_idx].set_ylabel('Speed (rad/s)')
                    if row_idx == 1:
                        ax_speed[row_idx, col_idx].set_xlabel('Time (s)')

                    #Plot observed values
                    ax_speed[row_idx, col_idx].plot(times, speeds, label = "Observed")

                    #Make predictions
                    predictions = filter.predict_batch(speeds)

                    #Plot predicted values
                    ax_speed[row_idx, col_idx].plot(times, predictions, label = "Filter")
            
            #Create legend, removing duplicate labels
            handles, labels = plt.gca().get_legend_handles_labels()
            by_label = dict(zip(labels, handles))
            fig_speed.legend(by_label.values(), by_label.keys())

            #Save figure, plot results. Start by replacing decimals in gains with underscores
            speed_filename = "Speed_Plot_Run_{}_PWM_{}_alpha{}.jpg".format(run, command, alpha)
            fig_speed.savefig(pth.join(speed_plot_path, speed_filename))

            plt.show()


if __name__ == "__main__":

    main()

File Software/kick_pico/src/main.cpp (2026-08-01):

/*
main.cpp

Author: Tyler Bartunek

Ultimately going to be the main project code since it uses the actual framework
of the project to send and receive messages.

Module options:
    1. BlinkEcho: blinks onboard LED when disconnected, LED solid and echos messages received via SPI.
    2. Wheels (coming soon): Two configs (A and B), moves a Mecanum wheel according to received instructions
*/

//#define and #include:
// #include "EchoDevice.h"
#include "Wheels.h"

#define MODULE_TYPE Wheels


/****************************Main Function  *******************************/
int main(void){
    // Uncomment for debugging, and #include <iostream> in relevant class definition header file
    stdio_init_all();  // initializes USB or UART stdout depending on config, for debug purposes
    sleep_ms(3000);

    MODULE_TYPE pico_device = MODULE_TYPE();

    //Once connected, continuously read the SPI input buffer and write to the transmit buffer
    while(true){
       pico_device.run();
    }

    return 0;
}

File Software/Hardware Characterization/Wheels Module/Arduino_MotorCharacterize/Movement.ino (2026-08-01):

void DriveMotor(int command) {
  /*
Drives motor according to DRV8871 datasheet,
with 0 representing assumed braking and 255 representing 
full speed ahead. 

Note that we toggle the direction by pulling one of
the inputs high. This is so when the other input goes
high, we enter the braking regime; when the other input
goes low we move in the intended direction. This is the
recommended approach by the datasheet for PWM operation.
*/
  if (command > 0) {  //Forward
    digitalWrite(MOTOR_IN1, HIGH);
    analogWrite(MOTOR_IN2, 255-abs(command)); //Motor driver does opposite, forward when low and break when high
  } else if (command == 0) {  //Brake
    digitalWrite(MOTOR_IN1, HIGH);
    digitalWrite(MOTOR_IN2, HIGH);
  } else {  //Reverse
    digitalWrite(MOTOR_IN2, HIGH);
    analogWrite(MOTOR_IN1, 255-abs(command));
  }
}

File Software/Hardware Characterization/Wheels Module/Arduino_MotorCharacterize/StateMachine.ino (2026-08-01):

int GetTrajectory(Trajectory &traj, TestData &data) {

  //Initialize output
  static int command = 0;
  static int newCommand = 0;
  int maxReplicates = 5;
  int sizeCommandArray = sizeof(availableCommands) / sizeof(availableCommands[0]);

  switch (traj.state) {

    case START:
      
      shuffleArray(availableCommands, sizeCommandArray);
      newCommand = availableCommands[0];
      traj.lastChangeTime = millis();
      traj.state = MOVE;

      break;

    case MOVE:

      command = newCommand;

      if (HasElapsed(traj.lastChangeTime, 15000)) {  //Wait 15 seconds before changing command value
        newCommand = GetNextCommand(traj, data, availableCommands, sizeCommandArray);
        traj.state = RESET;
      }

      break;

    case RESET:

      command = 0;

      if (HasElapsed(traj.lastChangeTime, 5000)){

        if (!traj.finished){
          MotorEncoder.write(0);
          traj.state = MOVE;
        }
        else{
          if (data.runNumber <= maxReplicates) {
          traj.finished = false;
          MotorEncoder.write(0);
          traj.state = START;
        } else {
          traj.state = STOP;
        }
        }
      }

      break;

    case STOP:
      command = 0;
  }

  return command;
}

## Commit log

2026-04-29 Updated README
    Updated the README to reflect changes in package structure and kinematic calculations.
2026-05-06 pico code syncs up with ros
2026-05-10 pico code passes echo test
2026-06-04 Update Print Guide, GUI changes
2026-06-04 Initial Wheels commit
2026-06-05 toggle buttons and main stacked window added
2026-06-08 Refactor MainWindow and RailCanvas; add SensorConfig and SLAM_Map widgets
2026-06-09 Add XML module and sensor definitions; update ControlWidget and MainWindow for new functionality
2026-06-09 Modified SensorConfig and RailCanvas to change settings windows based on xml file contents
